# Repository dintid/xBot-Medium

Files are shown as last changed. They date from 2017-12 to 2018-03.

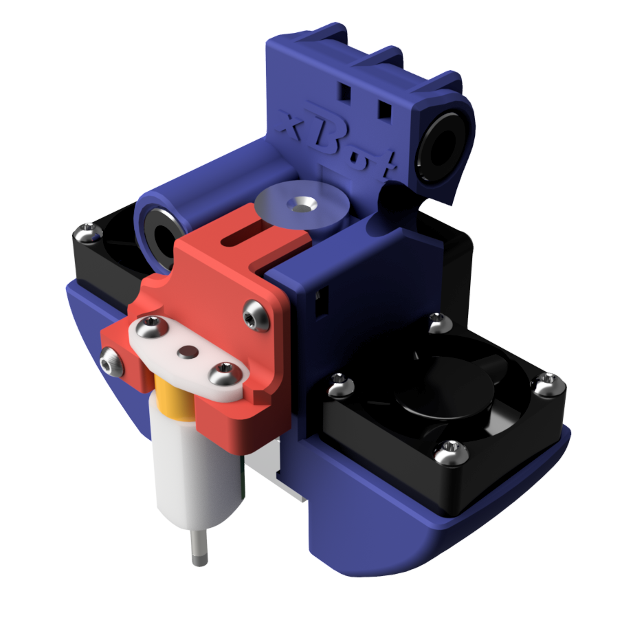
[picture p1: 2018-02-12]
Source files/Printed Parts/E3D carriage/Renders/xBot-Medium Carriage render front.png

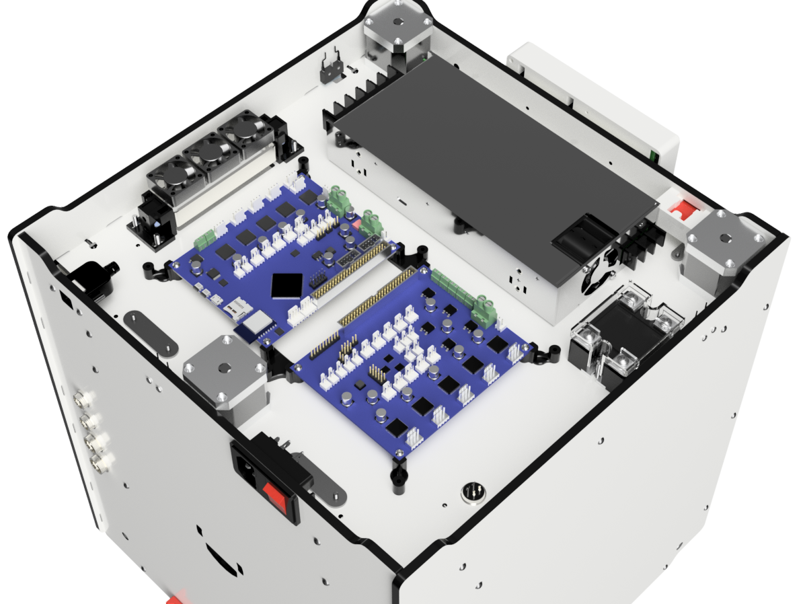
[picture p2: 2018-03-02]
Source files/Printed Parts/Printed Parts render/xBot Medium Bottom.png

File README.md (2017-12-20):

# xBot Medium
In this repository you will find the documentation and source files for the xBot Medium 3D printer. If you are missing a part or information on anything, please feel free to file an issue or contact me via my website at betrue3d.dk

Direct link to first descriptive blog-post:
https://betrue3d.dk/xbot-medium-a-new-printer-is-baking/

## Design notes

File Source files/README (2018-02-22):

Here you'll find all the custom source files for the project in .STP and .PDF format. 

The PDF files are mainly self explananatory while you will need the .STP files for the majority of the actual measurements.
Some PDF files contains information on threads, like the Z-gantry and brackets for the Z-rods.

The .STP files for the frame will be uploaded this week (week 8)

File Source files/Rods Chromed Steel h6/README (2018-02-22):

Here you'll find all the steel RODS we use for the xBot-Medium

The .STP files for the RODS are mostly just in place for the sake of it.

The PDF files contains all relevant measurements for the rods.

Do use some high quality Ground Steel h6 rods and not some generic "chromed steel" bars from china.

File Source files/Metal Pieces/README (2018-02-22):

The various metal/aluminium pieces are found in here.

I've intended the Motorshields to be made in material 0.5-1mm thickness. 
As long as the outer measurements are the same, the thickness doesn't really matter.

There are 2 different versions of the Z 8mm and Z 12mm endcaps:
I did this as it can be hard to find someone who can make these small pieces in steel.

1) First version are made up of 2mm thick steel brackets.
2) Second version are made up of 4mm thick aluminium brackets.

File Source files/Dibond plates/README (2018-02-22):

The plates used to build the frame of the xBot Medium printer

The PDF files are mostly descriptive in nature, where you'll use the .STP files for the actual measurements.

Remember there are lots of partical cuts, so you need a CNC facility who can handle this kind of compound material.

NOTE:
The Door for the front is a cut out part of the TOP frane piece.
The rear Z-Gantry shield is a cut out part of the FRONT frame piece.

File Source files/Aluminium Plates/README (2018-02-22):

# Custom aluminium parts for the xBot Medium printer:

Z-Stage/Z-Gantry lift plate
and
Optionally the Heated platform itself. 

You can use an Ultimaker 2 bed, as they have the same size. 

I recommend a nice AC silicone heater from Keenovo though. You can get them with build in Thermocoupler or PT100 sensor if you ask for it.
Keenovo have even talked about being able to build in PT1000 sensor, which doesn't require a daughterboard on the Duet!

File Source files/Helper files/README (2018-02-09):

In this directory you can find listings of various "other" items like dimensions and wiring of front LED, but also lenght and pin-layout of wiring harness to carriage and similar.
I will be creating these files as I finish them up as "final" and measure them up.

I can unveil the longest run of wireharness from the rear GX plugs up to carriage will be 100cm if you have configured your printer with the maxium distance possible, where you have a 3mm extruder placed at the opposite side of the GX connectors, so you have to route the wireharness across the printer and then along the Bowden tubing.
The 100cm is including the extra 5cm going into twisting the wires.

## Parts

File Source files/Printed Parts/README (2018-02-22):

Here you'll find the parts we need to print for the xBot-Medium printer.

You can also find these objects in a Collection I made on Thingiverse:
https://www.thingiverse.com/dintid/collections/xbot-3d-printer

I have tested and used all these objects.

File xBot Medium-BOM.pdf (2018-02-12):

## xBot-Medium BOM

by Morten Nielsen aka BeTrue3D and Dintid

## Bill Of Materials

All prices are approximate without shipping and will change over time.
The total price is the absolute highest possible price.
You can easily shave off €500 by using different heated bed, duex2 instead of duex5 etc.

Custom Parts:
https://betrue3d.dk/xbot-medium-look-at-materials-custom-bom/
Electronics and Electrical Parts https://betrue3d.dk/xbot-medium-electronics-and-electrical-parts-bom-cont/ Mechanical Parts
https://betrue3d.dk/xbot-medium-mechanical-parts-bom-cont/

## Parts for Dibond frame

Name | Amount | Price # | Price total | Total
xBot Back | 1 | € 45,00 | € 45,00
xBot Bottom | 1 | € 45,00 | € 45,00
xBot Front | 1 | € 45,00 | € 45,00
xBot Left | 1 | € 45,00 | € 45,00
xBot Right | 1 | € 45,00 | € 45,00
xBot Top | 1 | € 45,00 | € 45,00
Total | € 270,00 | € 270,00

## Steel Rods

Name | Amount | Price # | Price Total
X-Rods 8mm 367mm | 2 | € 5,02 | € 10,04
Y-Rods 8mm 358mm | 2 | € 4,90 | € 9,80
Z-Rods 8mm 339mm | 2 | € 4,66 | € 9,32
Z-Rods 12mm 339mm | 2 | € 5,66 | € 11,32
X-Rod 6mm 327mm | 1 | € 4,50 | € 4,50
Y-Rod 6mm 302mm | 1 | € 4,18 | € 4,18
Shipping DHL | 1 | € 19,00 | € 19,00
Total | € 68,16 | € 68,16

## Metal/steel Parts

Name | Amount | Price # | Price Total
Left Motorshield | 1 | € 0,00
Right Motorshield | 1 | € 0,00
Z-8mm Rod Plates* | 2 | € 0,00
Z-12mm Rod Plates* | 2 | € 0,00
* If you can't get steel brackets, you can use 4mm thick aluminium instead. See below

## Aluminium Parts

Name | Amount | Price # | Price Total
5mm PEI Coated printbed
257x229x5mm*
1 | € 54,00 | € 54,00

Z-Liftplate | 1 | € 45,00 | € 45,00
Total | € 99,00 | € 99,00
* You can use a heatbed from Ultimaker 2.

### Electronics and electrics

Name | Amount | Price # | Price Total
Duet Wifi | 1 | € 162,30 € 162,30
Duex 2/5* | 1 | € 116,60 € 116,60
Thermocoupler Daughterboard** | 1 | € 31,00 | € 31,00
PT100 Daughterboard | 1 | € 31,00 | € 31,00
PanelDue 4.3"*** | 1 | € 99,89 | € 99,89
BLTouch SMART | 1 | € 39,90 | € 39,90
Heated Bed**** | 1 | € 54,00 | € 54,00
AC Silicone heater 500w | 1 | € 40,50 | € 40,50
SSR DC-AC | 1 | € 4,00 | € 4,00
Chamber Heater 200w Ceramic PTC Heater | 1 | € 4,75 | € 4,75
24v 30mm fans for Chamber Heater | 3 | € 1,21 | € 3,63
12v 30mm Fans for Printed Objects | 2 | € 2,08 | € 4,16
Powersupply HPR-450-24 or similar | 1 | € 60,00 | € 60,00
LED - RGB | 1 | € 11,25 | € 11,25
Front USB Power 5v 3a | 1 | € 1,12 | € 1,12
Rear USB Port | 1 | € 1,79 | € 1,79
Total | € 665,89 | € 665,89
* Price listed is for Duex5
** You can do with just 1 and use Thermistor instead or even PT1000 (with 3x zeros) without daughterboard *** Not really necesary. There is not room for 7".
**** 5mm Aluplate or use UM2 heated bed.

### Various electrical mechanical parts

Name | Amount | Price # | Price Total
Manual on-off switch | 1 | € 1,00 | € 1,00
Limit Switch - Long Arm | 2 | € 1,12 | € 2,24
Limit Switch - Short Arm | 3 | € 1,15 | € 3,45
AC Power plug on/off | 1 | € 1,12 | € 1,12
GX12-2-pin | 1 | € 1,00 | € 1,00
GX12 4-pin | 6 | € 1,00 | € 6,00
GX12-5-pin | 1 | € 1,00 | € 1,00
GX16 8-pin | 1 | € 1,00 | € 1,00
GX16 6-pin | 1 | € 1,00 | € 1,00
GX16 5-pin | 1 | € 1,00 | € 1,00
Total | € 18,81 | € 18,81

## Motors

Name | Amount | Price # | Price Total

Nema 17 w. 280 lead screw
SKU: 17HS3001-280N
| 3 | € 26,70 | € 80,10
X and Y Motors SKU:17HM18- 2004S | 2 | € 11,90 | € 23,80
Extruder Motors * SKU:17HM18-2004S | 1 | € 11,90 | € 11,90
Extruder Motors * SKU:17HM08-1204S | 2 | € 9,90 | € 19,80
Total | € 135,60 | € 135,60
* For 2.85/3mm filament
** For 1,75mm filament

### Hotend and parts

Name | Amount | Price # | Price Total
E3Dv6 Full 1,75mm Bowden | 1 | € 63,60 | € 63,60
PT100 sensor | 1 | € 12,50 | € 12,50
Plated 0.4mm Copper Nozzle | 1 | € 11,75 | € 11,75
Heater Cartridge 40w | 1 | € 5,40 | € 5,40
Total | € 93,25 | € 93,25

### Mechanical Parts other

Name | Amount | Price # | Price Total
200GT-2 Belts | 2 | € 0,33 | € 0,66
20-GT2 Pulley 5mm Bore | 2 | € 1,33 | € 2,66
20-GT2 Pulley 8mm Bore | 10 | € 0,66 | € 6,60
610-GT2 Belts | 4 | € 0,75 | € 2,98
Sliders å bushing + spring | 4 | € 2,15 | € 8,60
Bag of Spacers 8mm Bore | 1 | € 4,70 | € 4,70
F688 Flanged Bearings | 8 | € 0,42 | € 3,32
Anti Backblash Nut | 3 | € 2,49 | € 7,46
LMK12LUU Flanged Bearings | 2 | € 2,32 | € 4,64
LM8UU Flanged Bearings | 2 | € 2,07 | € 4,14
Fingerscrews sets of fingerscrew, spring, spacer | 3 | € 1,13 | € 3,39
LM6LUU | 2 | € 1,58 | € 3,16
Total | € 52,31 | € 52,31

### Screws, Nuts Etc

Name | Amount | Price # | Price Total
m3 8mm Button Head | 10
m3 10mm Button Head | 64
m3 10mm Socket Head | 4
m3 12mm Button Head | 21
m3 16mm Button Head | 61
m3 20mm Button Head | 6
m3 30mm Button Head | 8
m3 20mm Flat Head (countersunk) | 3
m3 Spacer | 8

m3 Square Nuts | 45
m3 Nuts

4
m4 10mm Button Head

4
m4 12mm Button Head

8
m4 20mm Button Head

6
m4 Spacer

8
Wires
Connectors
Heatshrink
Wirewrap
Total Approximate | € 40,00 | € 40,00
Totalling: | | € 1.443,02

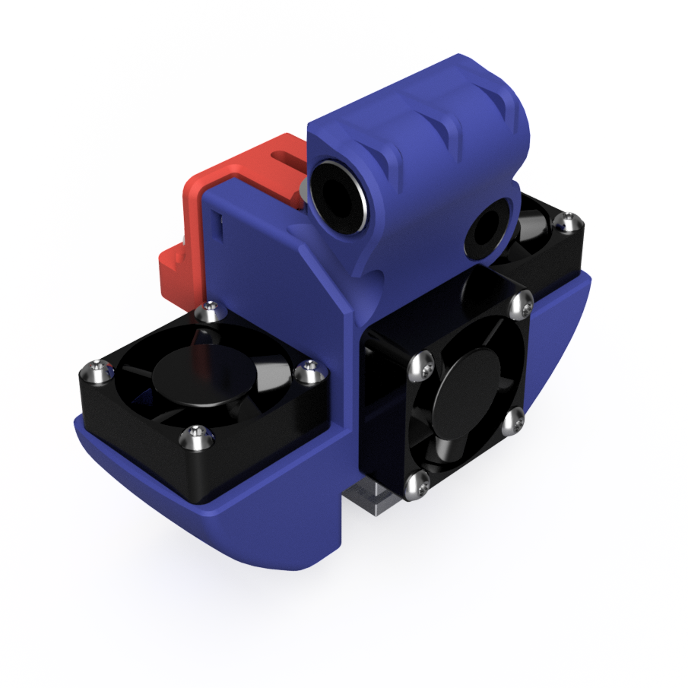
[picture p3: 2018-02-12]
Source files/Printed Parts/E3D carriage/Renders/xBot-Medium Carriage render rear.png

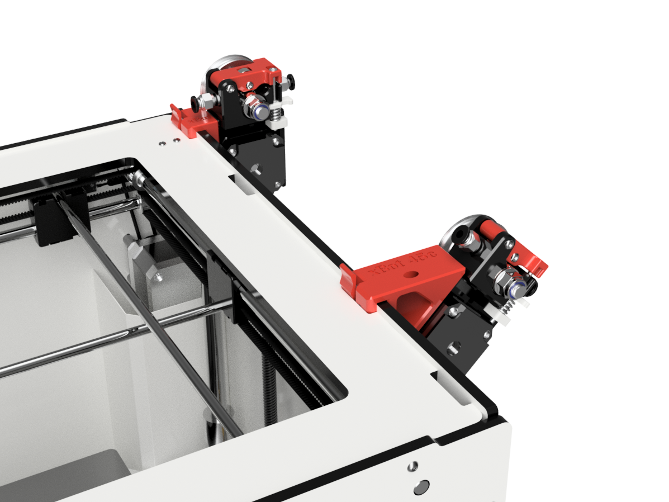
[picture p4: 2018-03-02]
Source files/Printed Parts/Printed Parts render/xBot Medium Clip-On-show.png

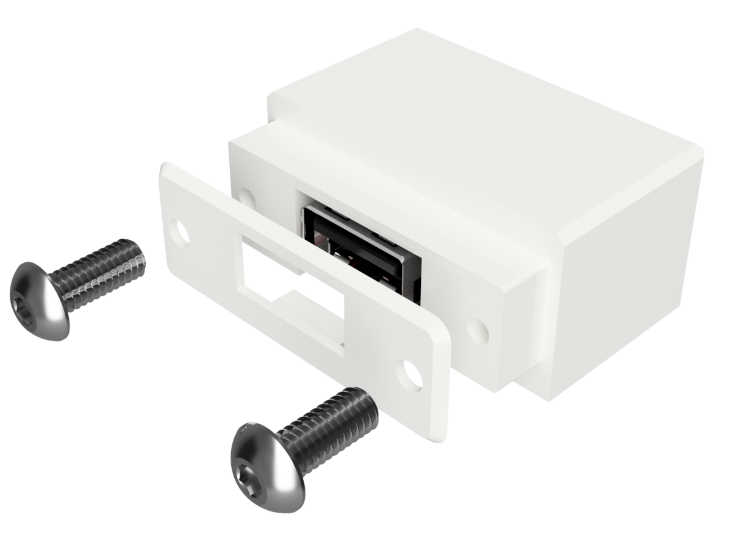
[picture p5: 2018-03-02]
Source files/Printed Parts/Printed Parts render/USB front mount v8.png

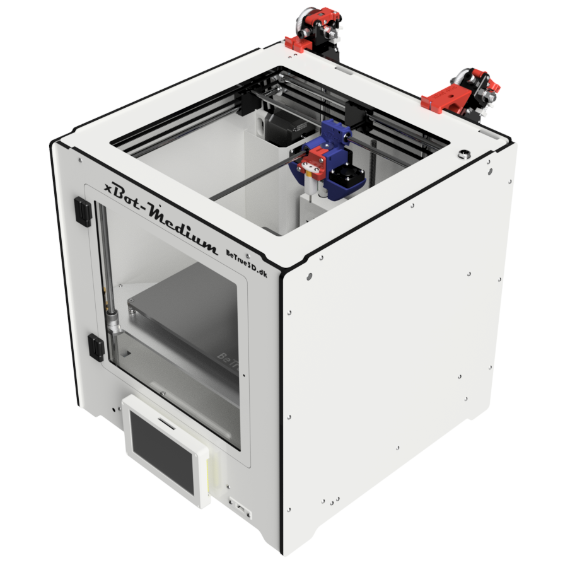
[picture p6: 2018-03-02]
Source files/Printed Parts/E3D carriage/xBot Medium render mid feb.png

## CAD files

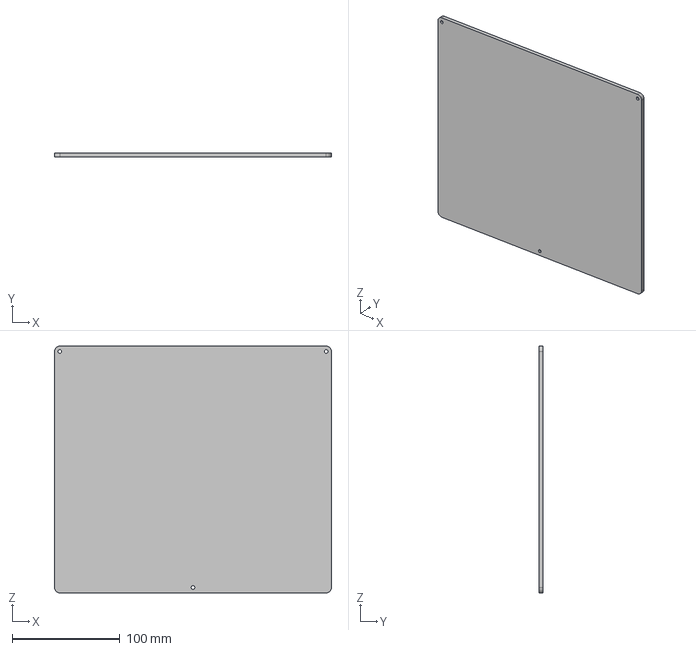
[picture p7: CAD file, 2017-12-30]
Source files/Aluminium Plates/Heatplate.stp
257.0 x 4.00 x 229.0 mm

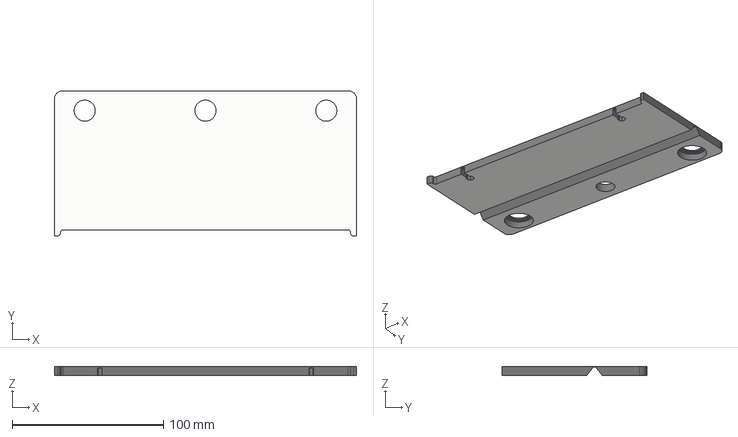
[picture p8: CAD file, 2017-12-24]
Source files/Dibond plates/Z-Rod Shield Rear - Reference only.stp
200.0 x 96.0 x 6.00 mm

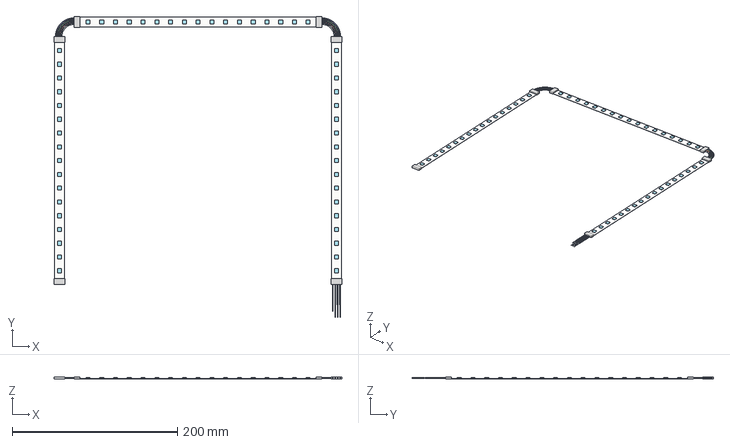
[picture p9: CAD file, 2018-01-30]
Source files/Helper files/xBot Medium - Front LED.stp
348.5 x 364.3 x 3.00 mm

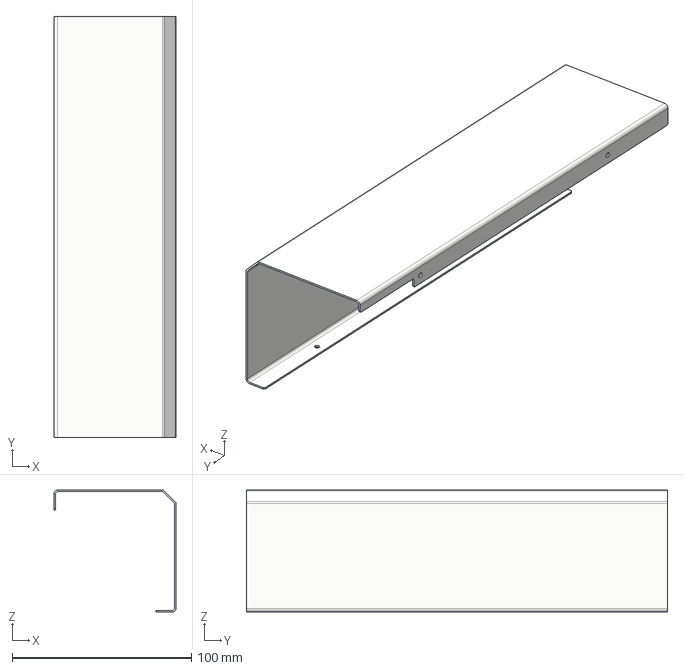
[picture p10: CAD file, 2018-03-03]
Source files/Metal Pieces/MotorShield x2.step
68.0 x 235.0 x 68.0 mm

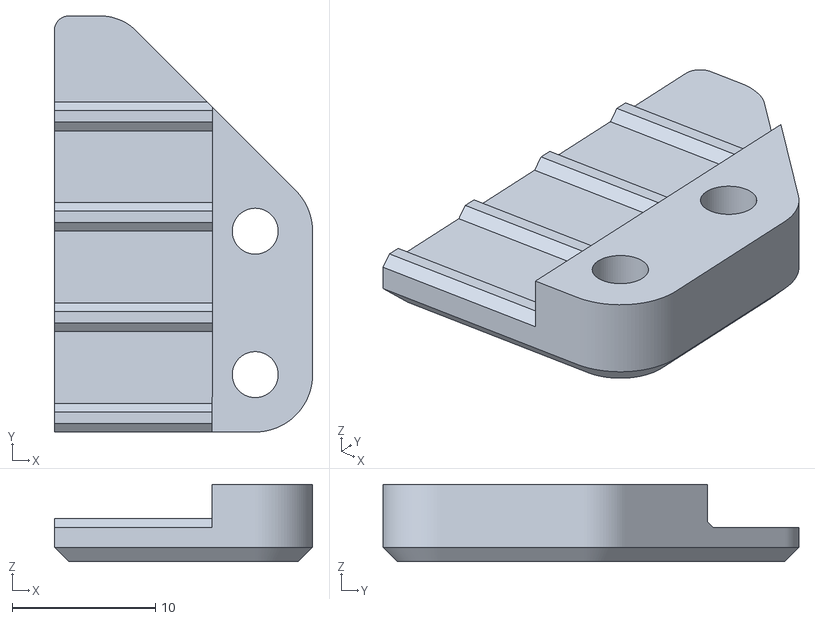
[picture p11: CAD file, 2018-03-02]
Source files/Printed Parts/Bed Wire Relief/Bed-Wire Relief.stl
18.0 x 29.0 x 5.40

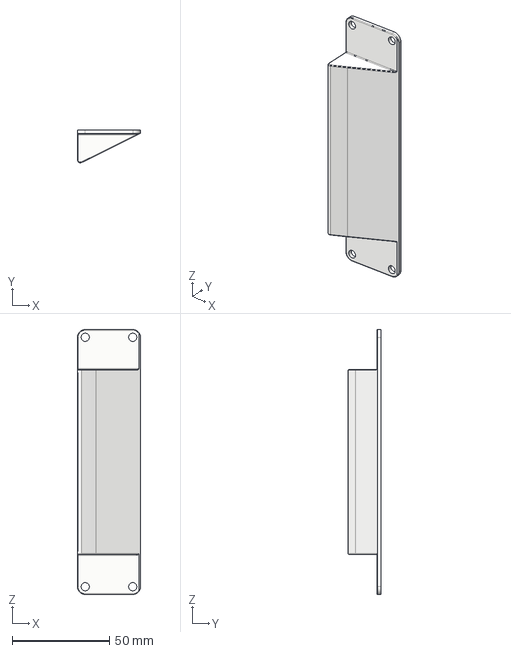
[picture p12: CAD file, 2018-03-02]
Source files/Printed Parts/Chamber Heater/Chamber heater fanduct.stp
32.4 x 16.8 x 136.0 mm

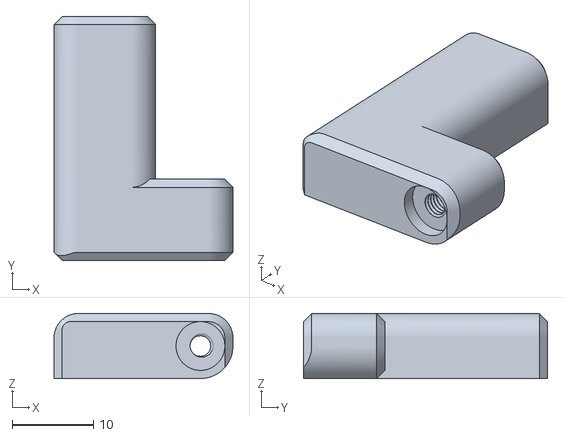
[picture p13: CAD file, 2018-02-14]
Source files/Printed Parts/Door Hinges/Hinge Frame.stl
22.0 x 30.0 x 8.00

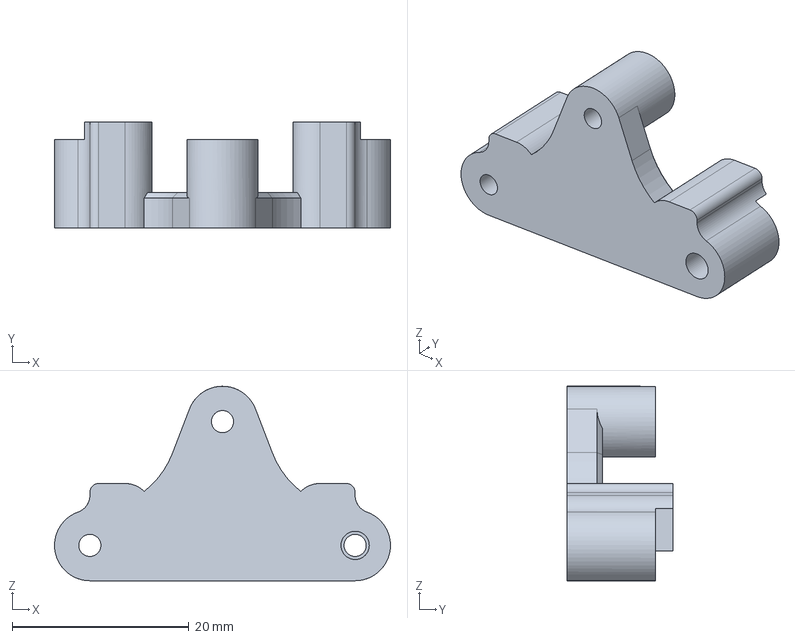
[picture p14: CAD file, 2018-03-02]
Source files/Printed Parts/Duet-Duex Mounting parts/DuetDuex xBot Mounting x2.stp
38.0 x 12.0 x 22.0 mm

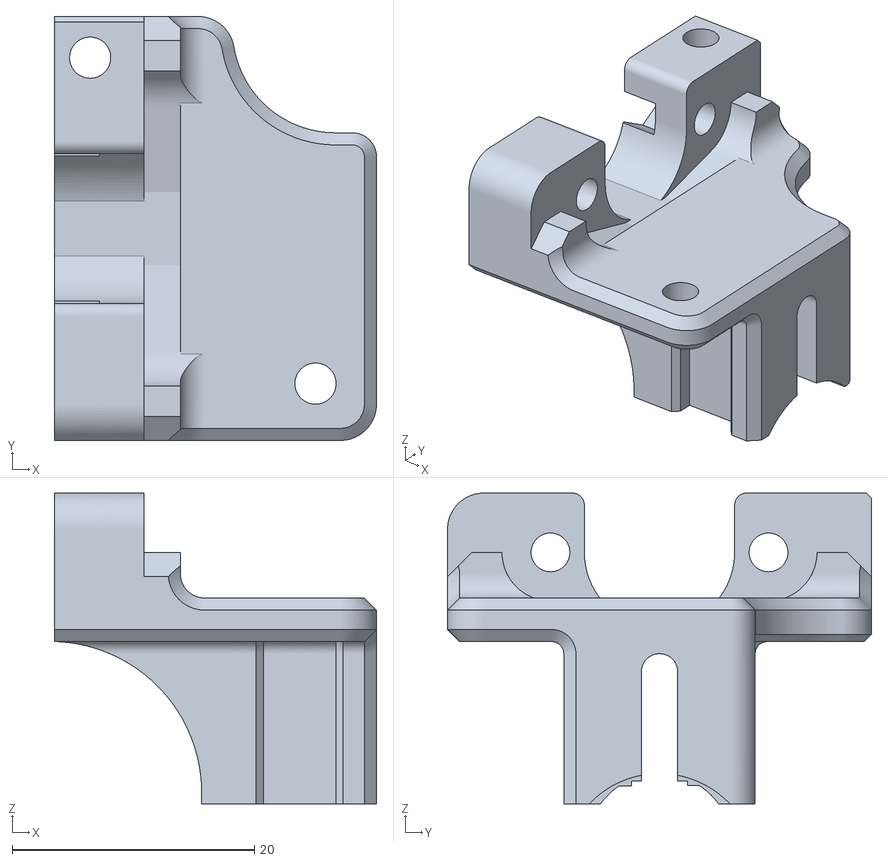
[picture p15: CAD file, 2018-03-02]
Source files/Printed Parts/E3D carriage/xBot BLTouch-Mount_Hotend-Clamp.stl
26.6 x 35.0 x 25.7

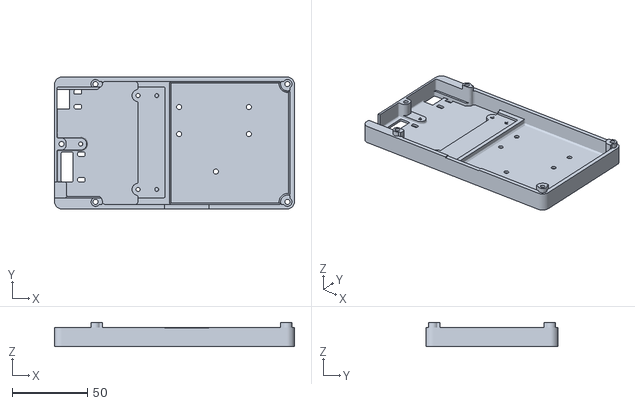
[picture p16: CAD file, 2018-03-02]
Source files/Printed Parts/PD5 Compact w hidden wires for v2 and v3 PCB/PD5 Compact Back w hidden wires for v2 and v3 PCB.stl
159.9 x 87.9 x 16.3

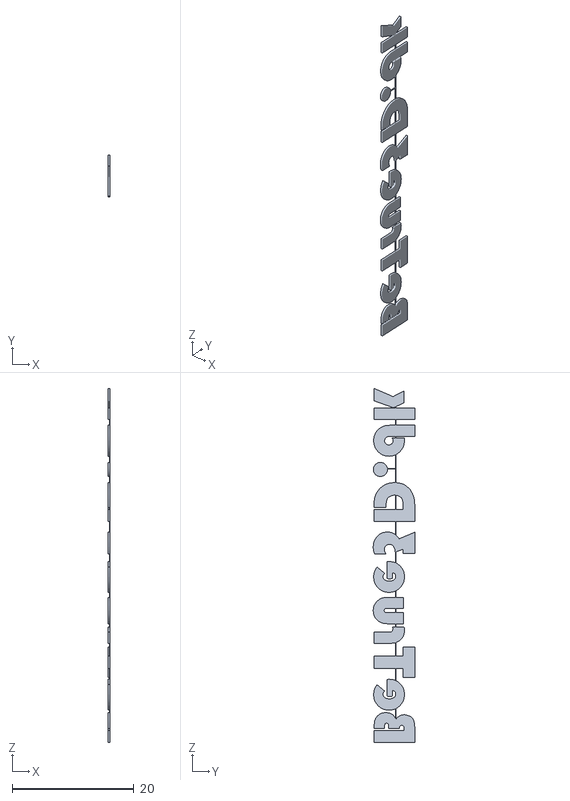
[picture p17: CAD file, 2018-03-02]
Source files/Printed Parts/Text/BeTrue3D.stl
0.3 x 6.83 x 58.0

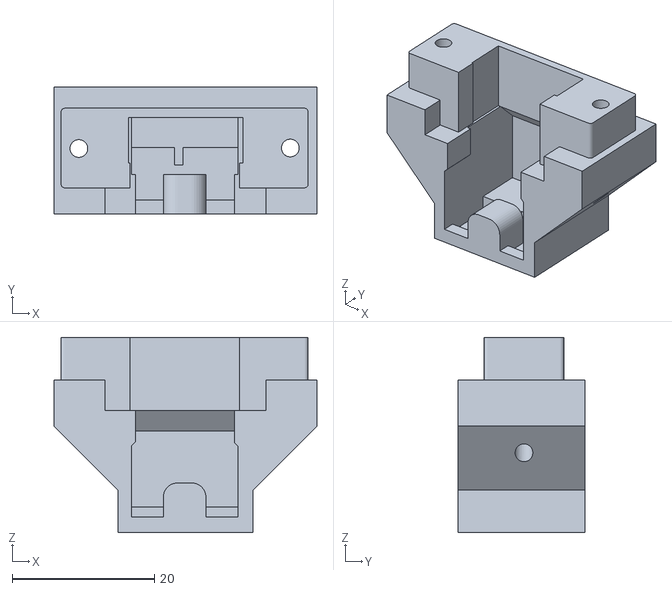
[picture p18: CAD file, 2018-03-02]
Source files/Printed Parts/USB Mount front/USB Front Mount -Inside.stl
37.0 x 17.9 x 27.5

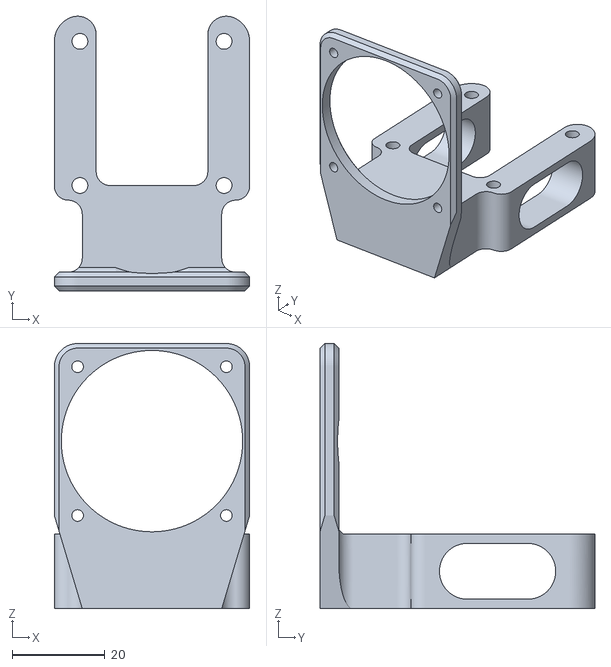
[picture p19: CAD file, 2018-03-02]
Source files/Printed Parts/XY Motor mounts/XY Motor Mount w fan.stl
42.0 x 59.1 x 57.0

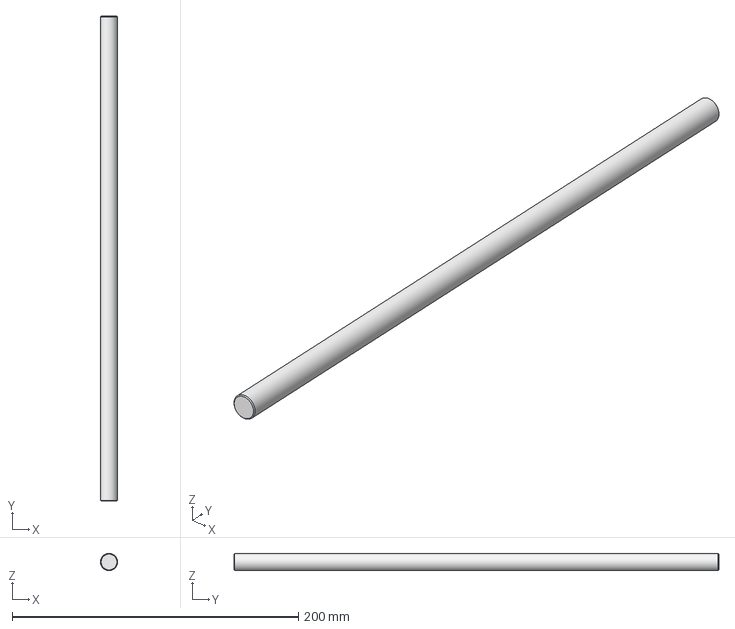
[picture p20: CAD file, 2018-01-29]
Source files/Rods Chromed Steel h6/Z-12mm_339mm rods x2.stp
12.0 x 339.0 x 12.0 mm

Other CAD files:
Source files/Aluminium Plates/Z-Lift Plate xBot Medium.stp
Source files/Metal Pieces/Z-8mm Rod-Plates - 4mm thick alux2.stp
Source files/Printed Parts/Chamber Heater/Guard-Chamber Heater and FanShroud for x3 Fans.stp
Source files/Metal Pieces/Z-12mm rod-plates - 4mm thick alu x2.stp
Source files/Metal Pieces/Z-12mm rod-plates x2.stp
Source files/Metal Pieces/Z-8mm Rod-Plates x2.stp
Source files/Printed Parts/Chamber Heater/Chamber heater fanduct.stl
Source files/Printed Parts/Chamber Heater/Guard-Chamber Heater and FanShroud for x2 Fans.stl
Source files/Printed Parts/Chamber Heater/Guard-Chamber Heater and FanShroud for x3 Fans.stl
Source files/Printed Parts/Door Hinges/Hinge Door.stl
Source files/Printed Parts/Door Hinges/Hinge-Door.stl
Source files/Printed Parts/Door Hinges/Hinge-Frame.stl
Source files/Printed Parts/Duet-Duex Mounting parts/CableHookPSU.stl
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

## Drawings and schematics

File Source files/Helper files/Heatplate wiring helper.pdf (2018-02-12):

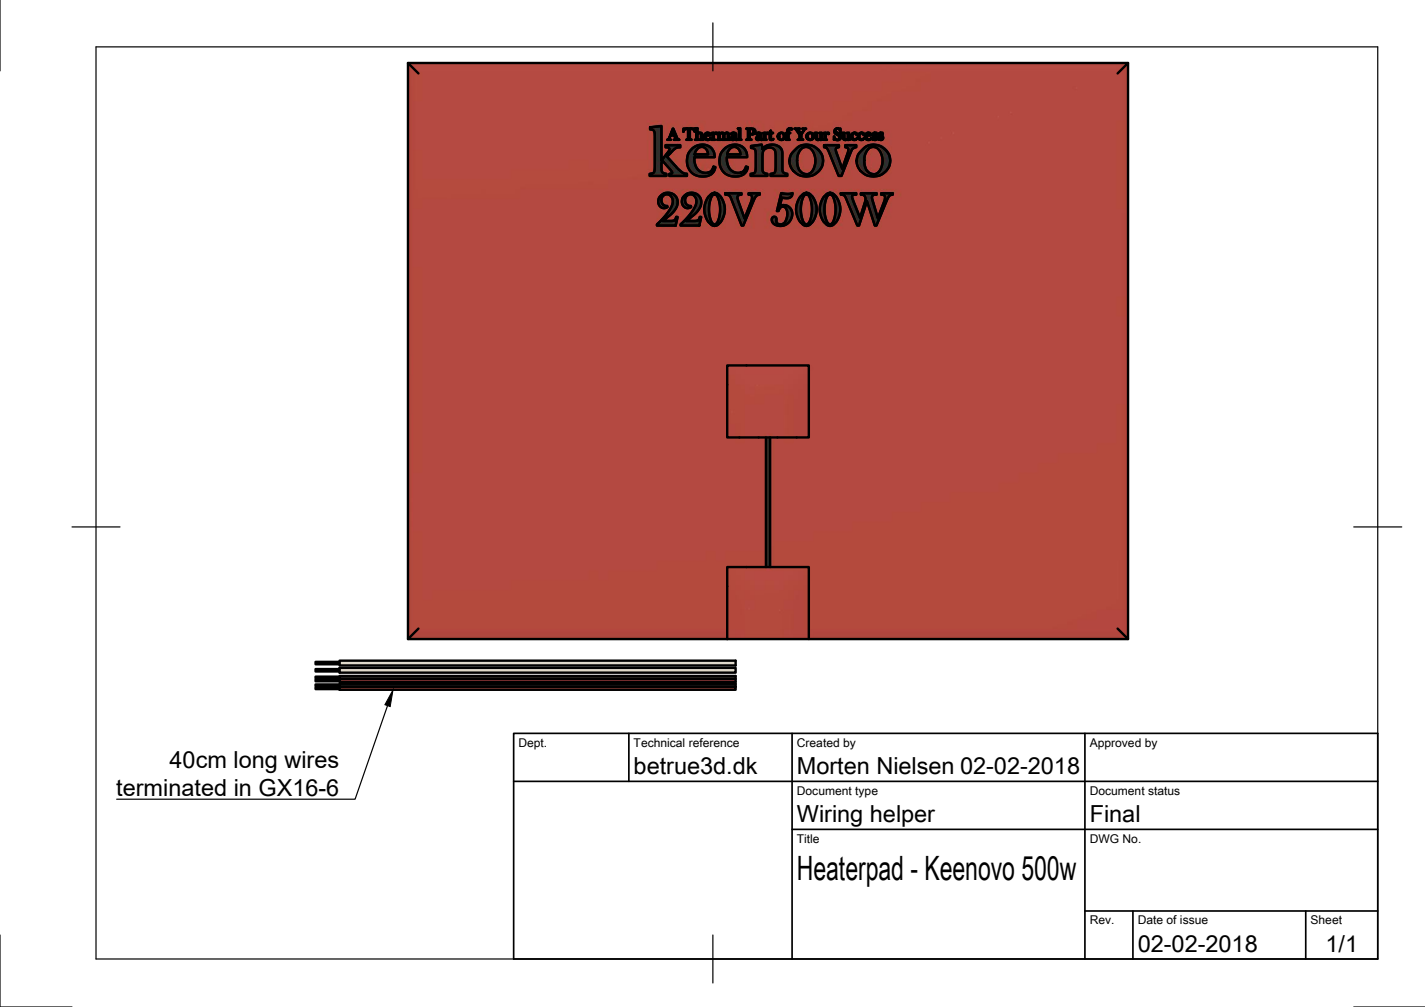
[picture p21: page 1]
terminated in GX16-6

Dept. | Technical reference betrue3d.dk | Created by Morten Nielsen 40cm long wires 02-02-2018 | Approved by

Document type Wiring helper | Document status Final

Title Heaterpad - Keenovo 500w | DWG No.

Rev. | Date of issue 02-02-2018 | Sheet 1/1

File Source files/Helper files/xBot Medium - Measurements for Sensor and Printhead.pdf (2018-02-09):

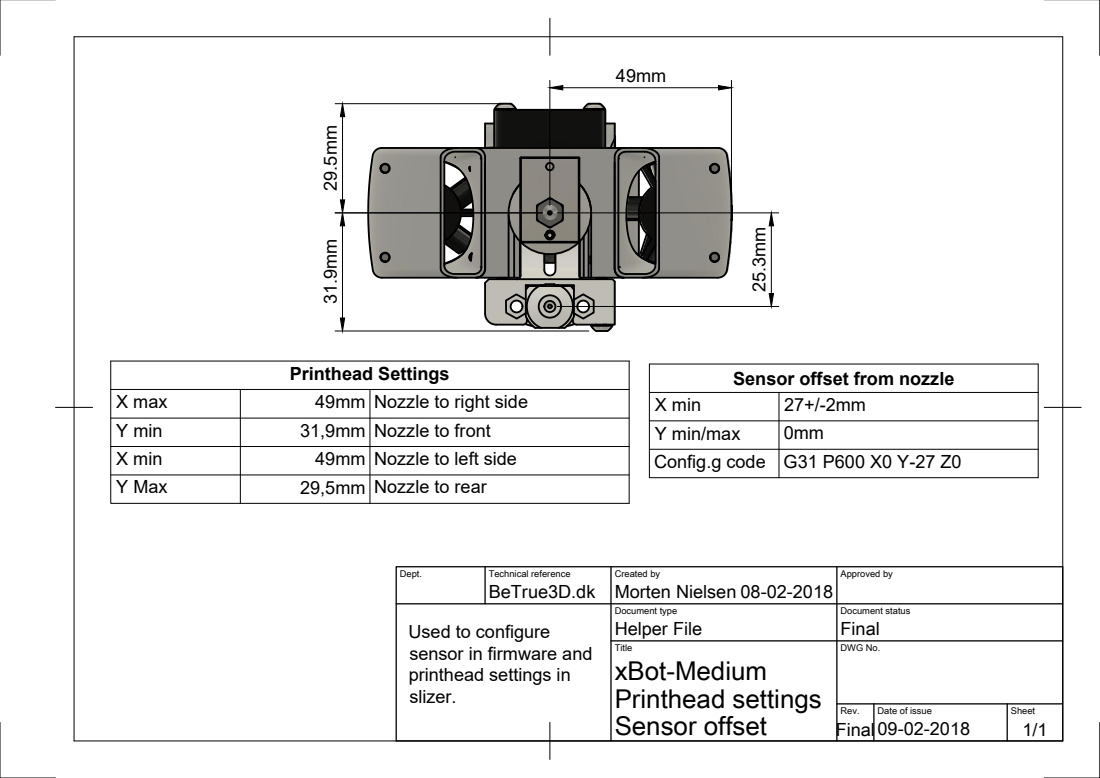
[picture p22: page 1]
BeTrue3D.dk; Morten Nielsen 25.3mm; Printhead Settings; X max; Nozzle to right side; Y min; Nozzle to front; X min; Y min/max

Sensor offset from nozzle

X min | 49mm | Nozzle to left side
Y Max | 29,5mm | Nozzle to rear

Config.g code | G31 P600 X0 Y-27 Z0

Dept. | Technical reference | Created by 08-02-2018 | Approved by

Used to configure sensor in firmware and printhead settings in slizer. | | Document type Helper File | Document status Final

Title xBot-Medium Printhead settings Sensor offset | DWG No.

Rev. Final 09-02-2018 | Date of issue | Sheet 1/1

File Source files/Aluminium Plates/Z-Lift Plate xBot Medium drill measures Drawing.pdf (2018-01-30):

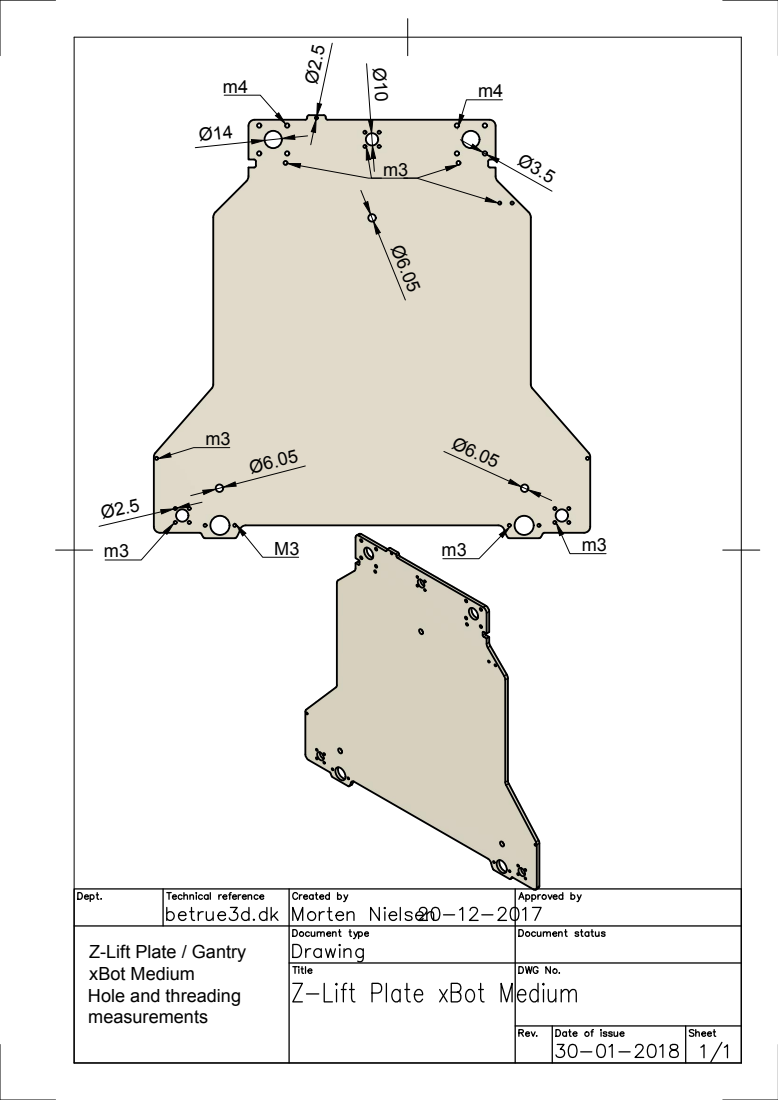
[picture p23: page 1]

Z-Lift Plate / Gantry
xBot Medium
Hole and threading
measurements

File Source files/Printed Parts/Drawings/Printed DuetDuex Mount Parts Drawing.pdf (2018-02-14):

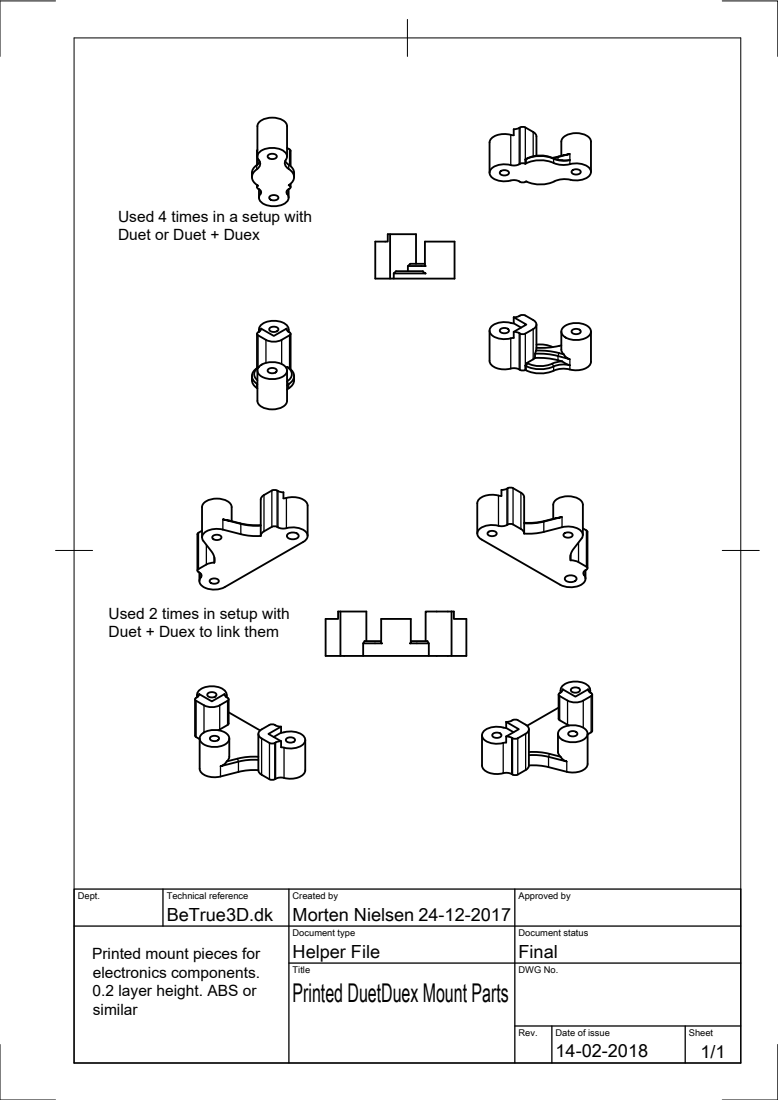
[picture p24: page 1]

Used 4 times in a setup with
Duet or Duet + Duex

Used 2 times in setup with
Duet + Duex to link them

Dept. | Technical reference BeTrue3D.dk | Created by Morten Nielsen 24-12-2017 | Approved by

Printed mount pieces for electronics components. 0.2 layer height. ABS or similar | | Document type Helper File | Document status Final

Title Printed DuetDuex Mount Parts | DWG No.

Rev. | Date of issue 14-02-2018 | Sheet 1/1

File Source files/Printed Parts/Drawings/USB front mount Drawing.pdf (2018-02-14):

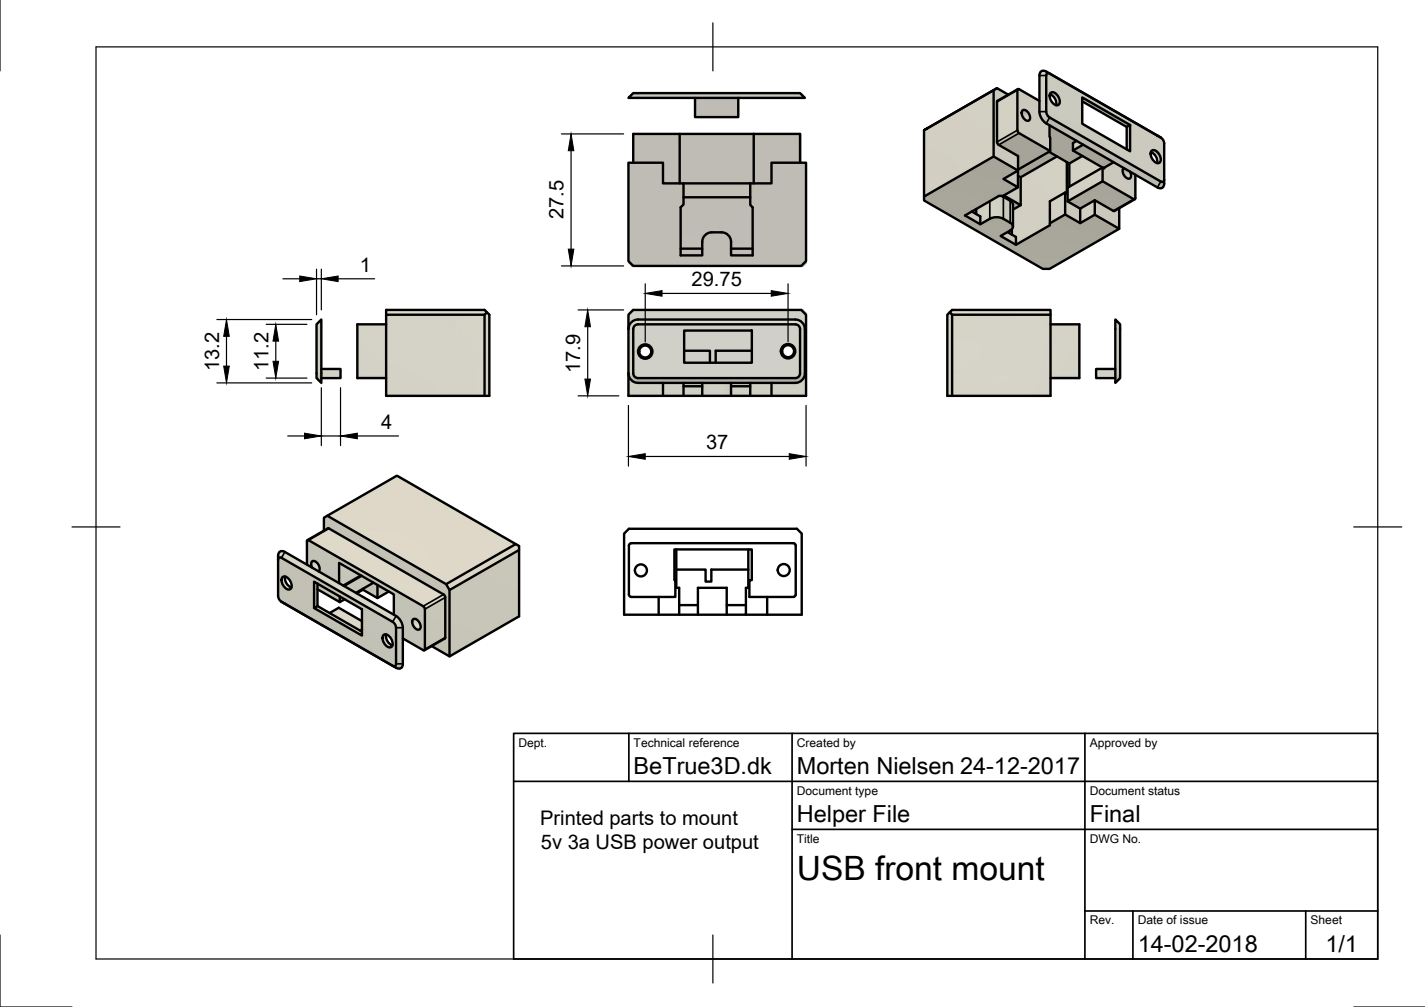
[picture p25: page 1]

Dept. | Technical reference BeTrue3D.dk | Created by Morten Nielsen 24-12-2017 | Approved by

Printed parts to mount 5v 3a USB power output | | Document type Helper File | Document status Final

Title USB front mount | DWG No.

Rev. | Date of issue 14-02-2018 | Sheet 1/1

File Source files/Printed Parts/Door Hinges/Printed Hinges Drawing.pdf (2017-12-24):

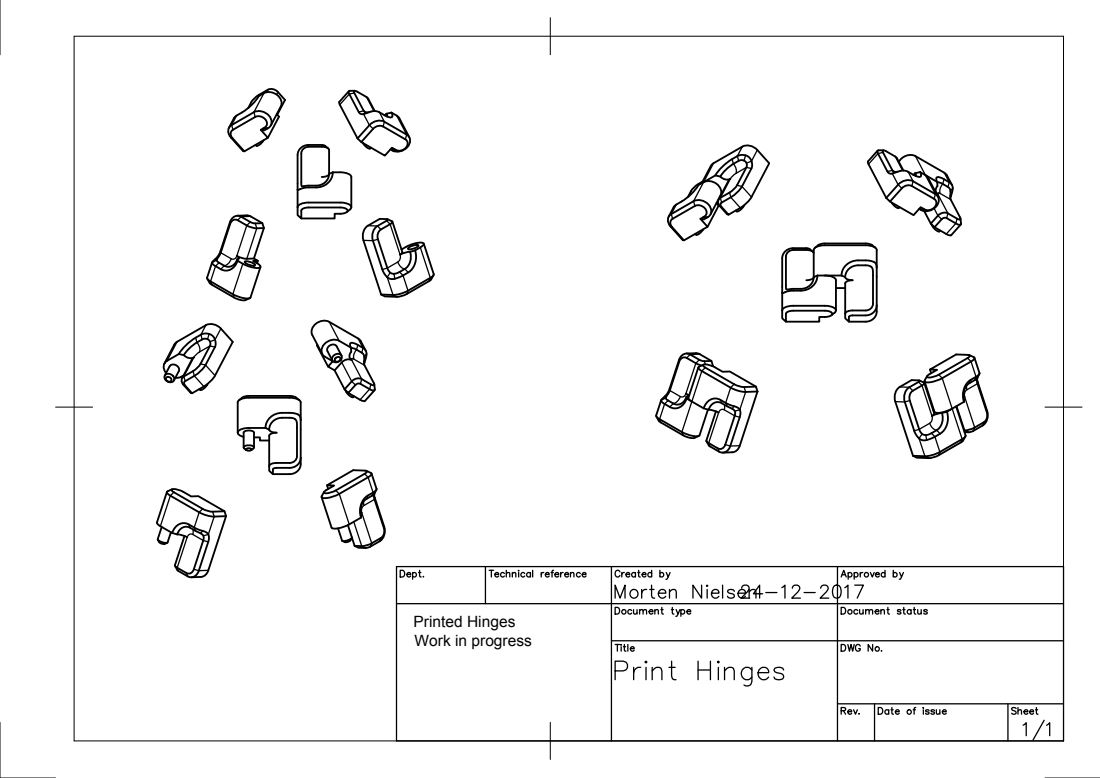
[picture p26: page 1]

Printed Hinges
Work in progress

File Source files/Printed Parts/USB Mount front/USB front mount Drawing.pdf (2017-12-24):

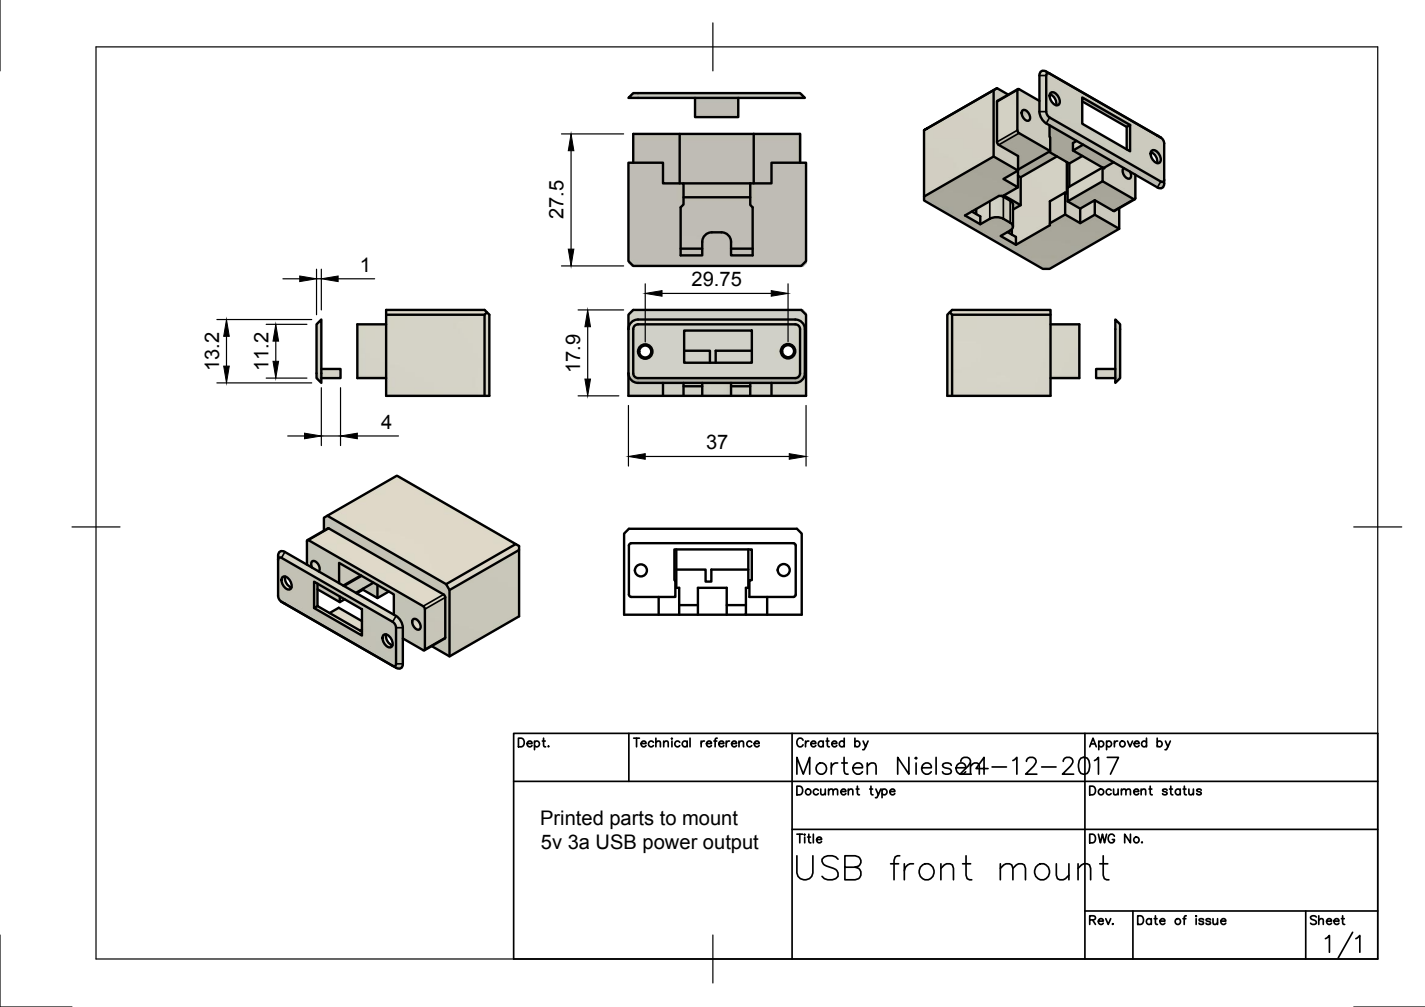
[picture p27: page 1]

Printed parts to mount
5v 3a USB power output

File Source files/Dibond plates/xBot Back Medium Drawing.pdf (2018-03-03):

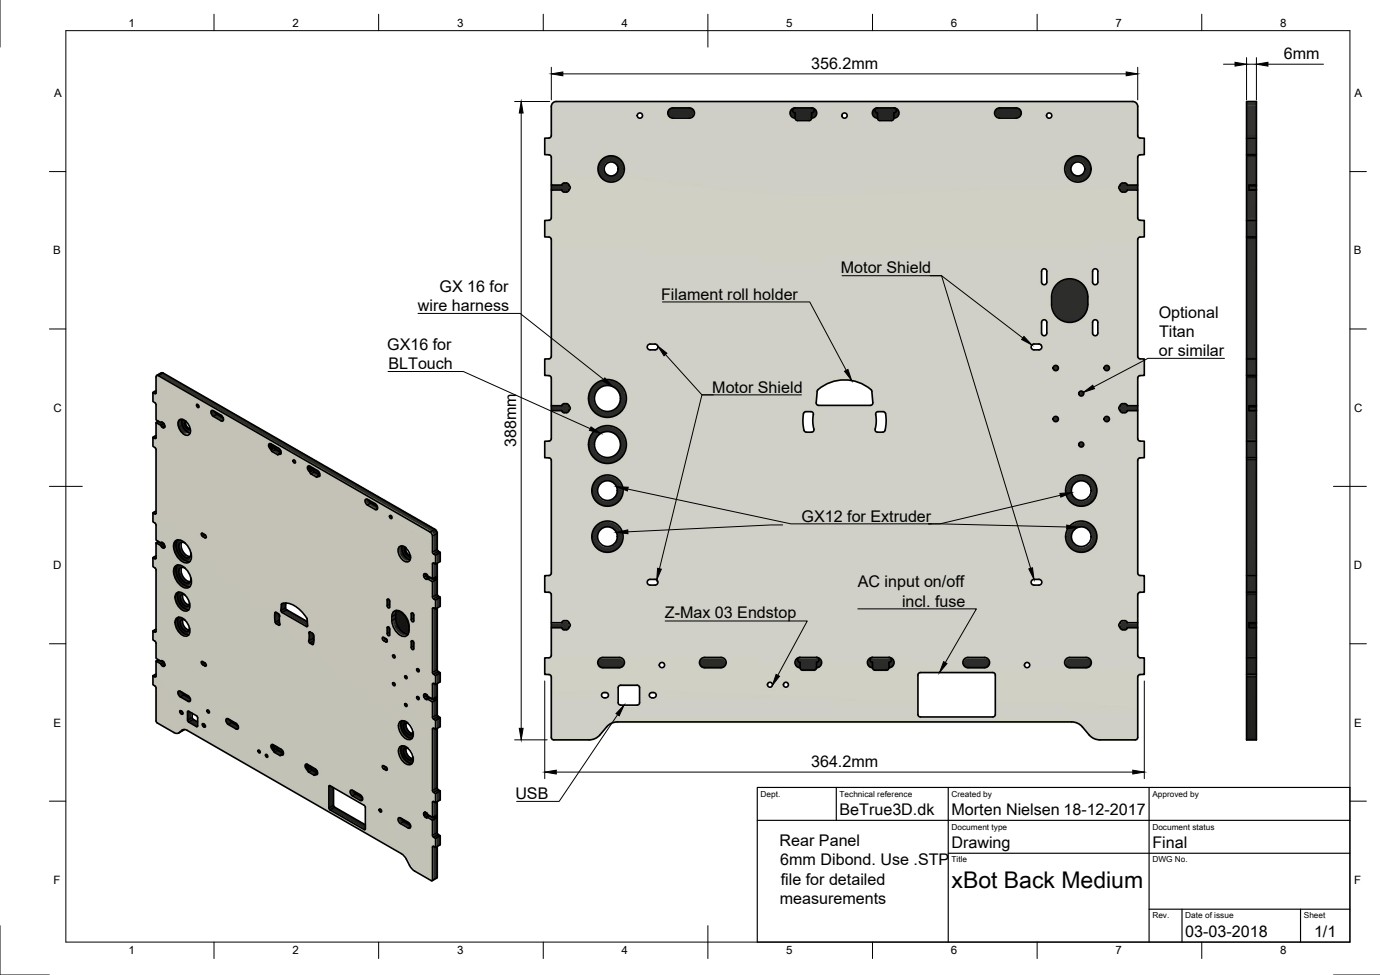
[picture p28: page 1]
or similar; GX 16 for wire harness; GX16 for; GX12 for Extruder; Motor Shield

Filament roll holder

AC input on/off

incl. fuse Z-Max 03 Endstop

Dept. | Technical reference BeTrue3D.dk | Created by Morten Nielsen 18-12-2017 | Approved by

Rear Panel 6mm Dibond. Use .STP file for detailed measurements | | Document type Drawing | Document status Final

Title xBot Back Medium | DWG No.

Rev. | Date of issue 03-03-2018 | Sheet 1/1

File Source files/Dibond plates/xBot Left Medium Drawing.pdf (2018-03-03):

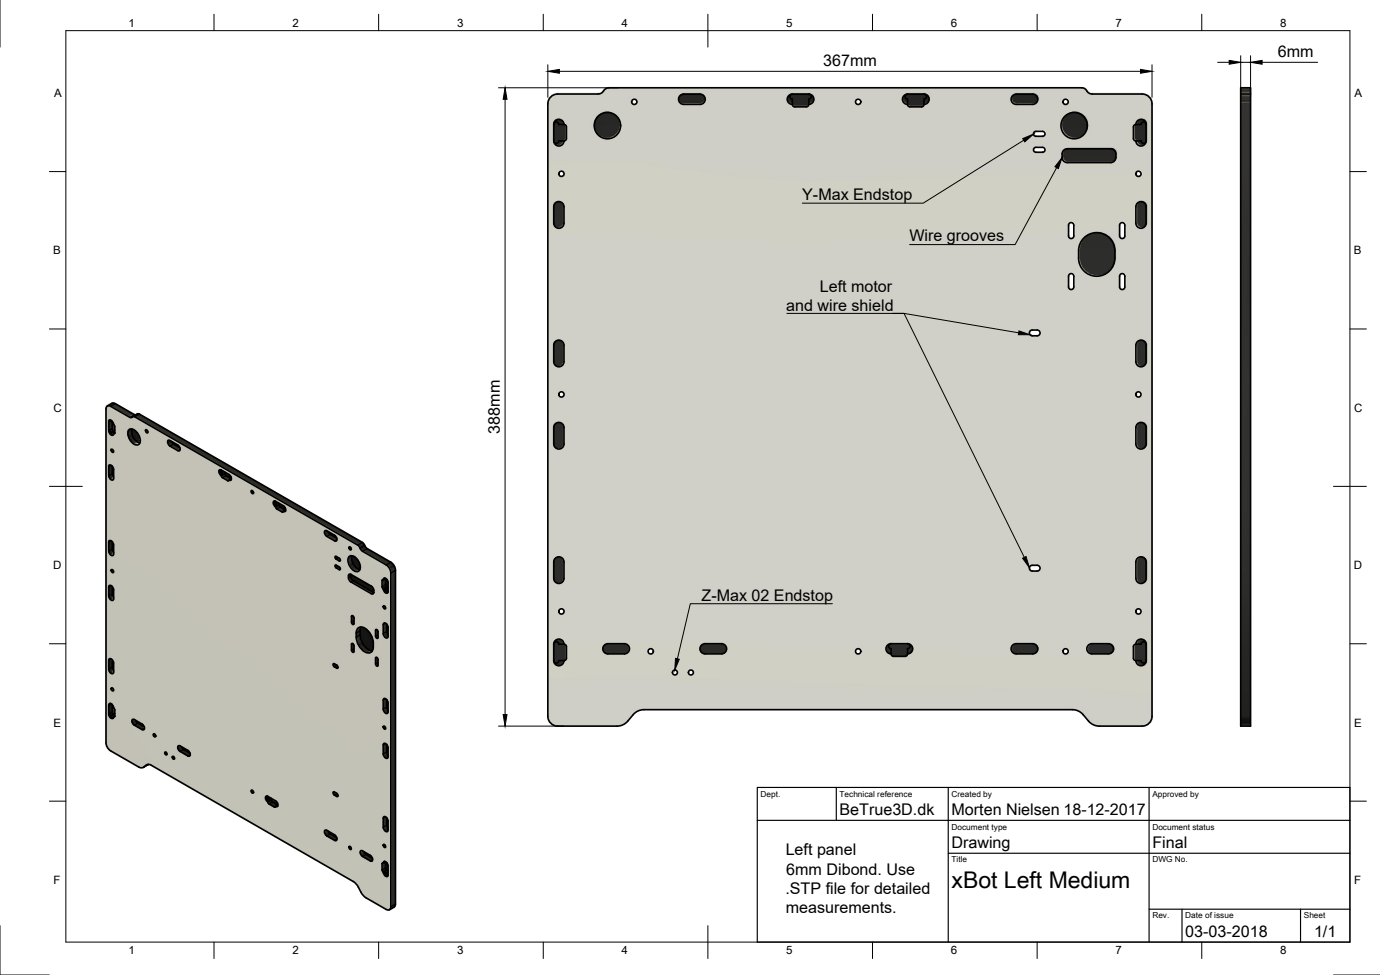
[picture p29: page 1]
BeTrue3D.dk; Morten Nielsen 388mm; Z-Max 02 Endstop; Y-Max Endstop; Wire grooves

Left motor
and wire shield

Dept. | Technical reference | Created by 18-12-2017 | Approved by

Left panel 6mm Dibond. Use .STP file for detailed measurements. | | Document type Drawing | Document status Final

Title xBot Left Medium | DWG No.

Rev. | Date of issue 03-03-2018 | Sheet 1/1

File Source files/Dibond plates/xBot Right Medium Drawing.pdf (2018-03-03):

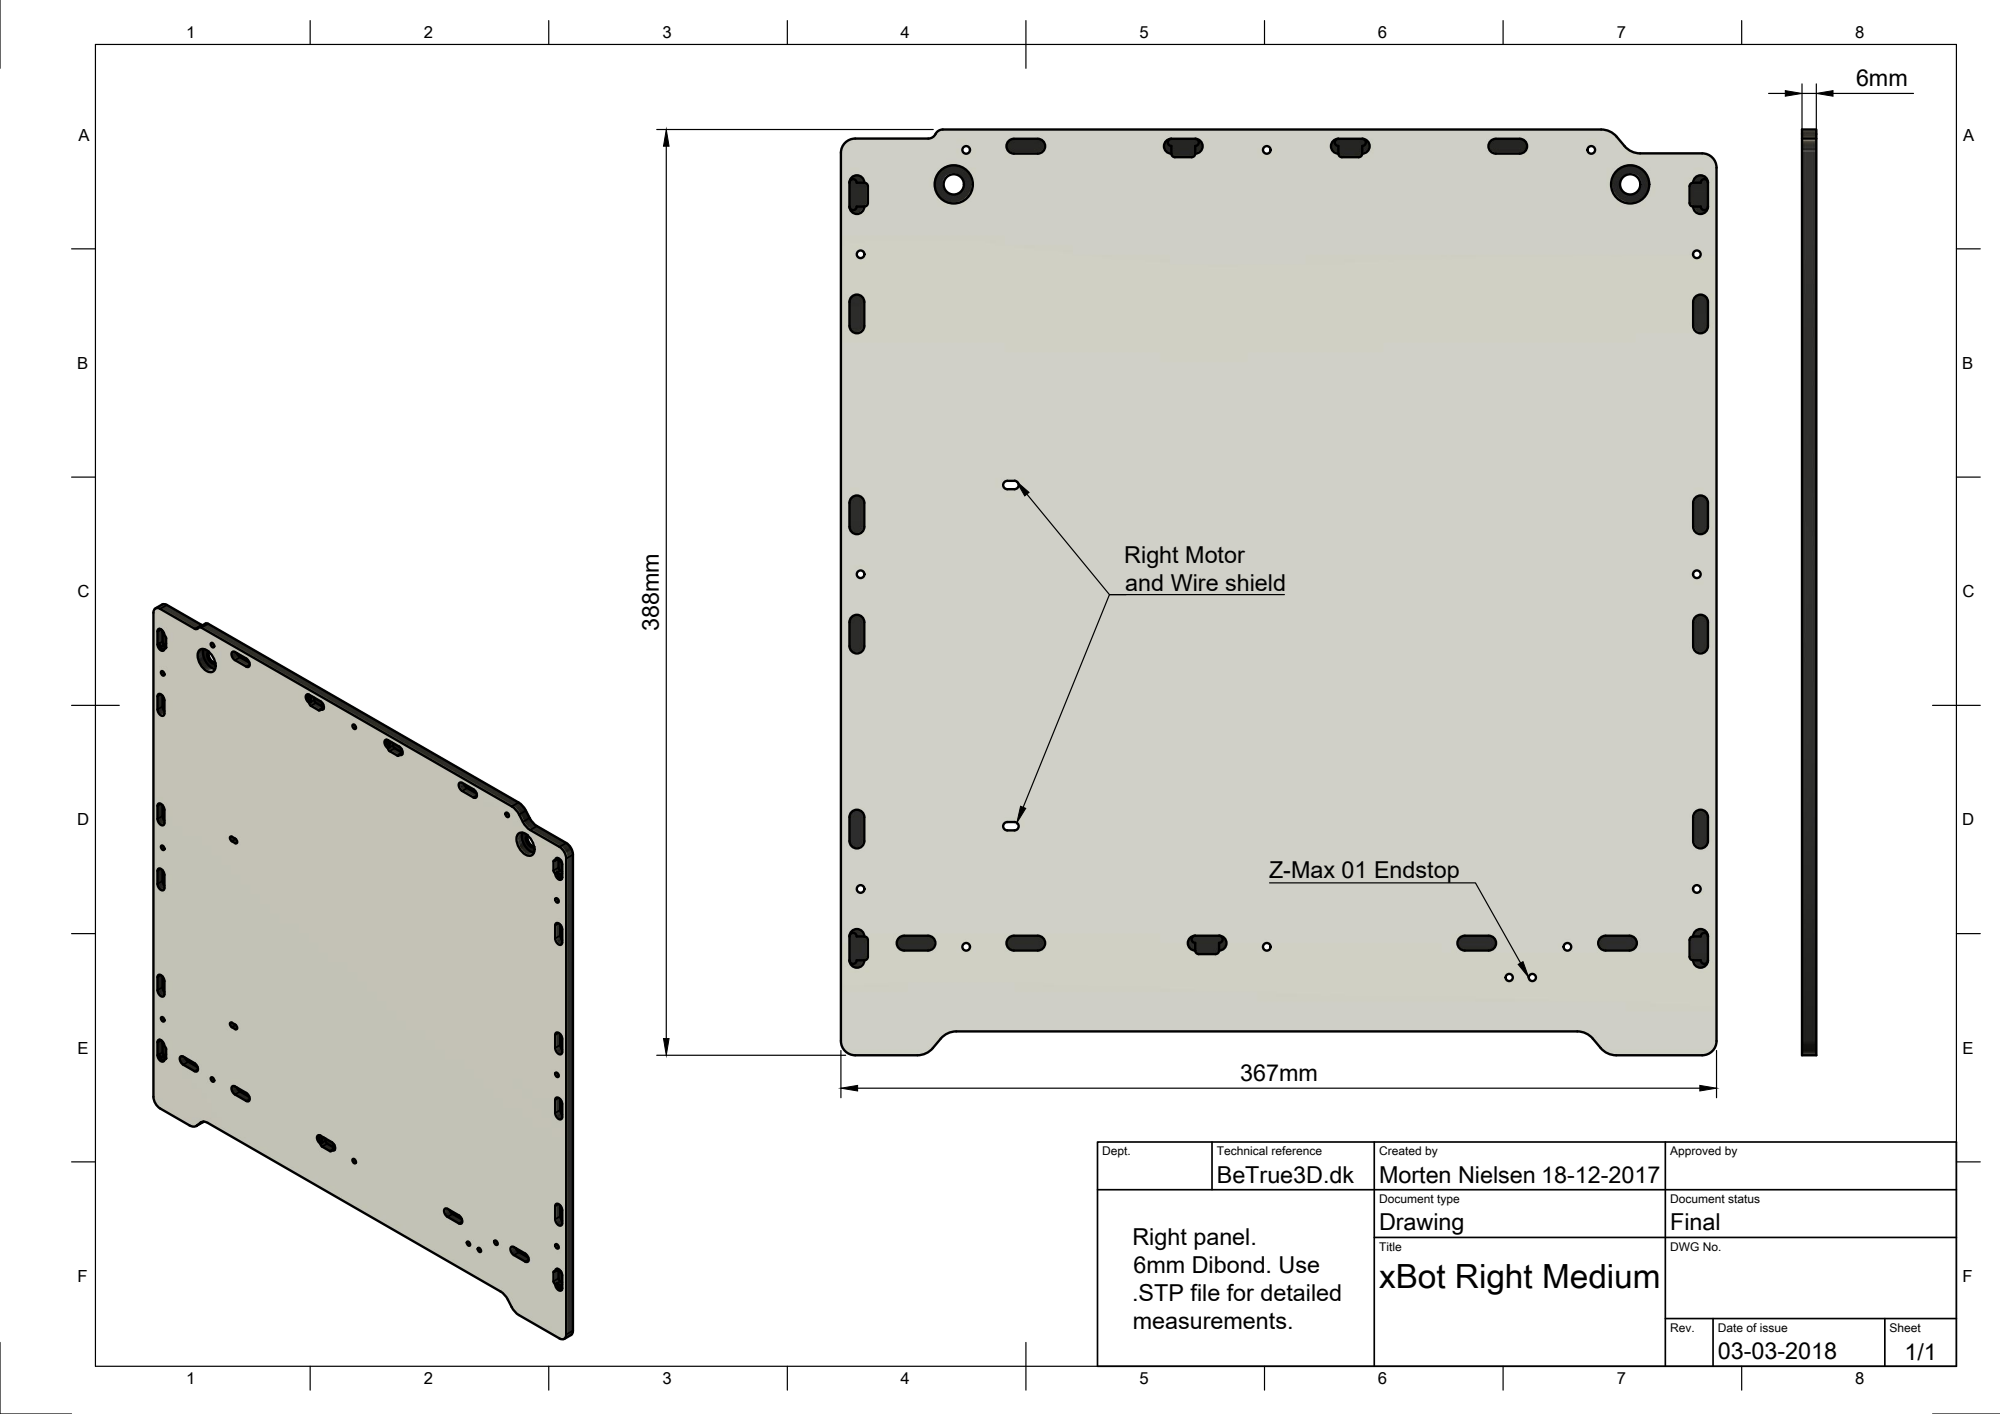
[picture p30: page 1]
BeTrue3D.dk; Morten Nielsen 388mm; Right Motor; Z-Max 01 Endstop

and Wire shield

Dept. | Technical reference | Created by 18-12-2017 | Approved by

Right panel. 6mm Dibond. Use .STP file for detailed measurements. | | Document type Drawing | Document status Final

Title xBot Right Medium | DWG No.

Rev. | Date of issue 03-03-2018 | Sheet 1/1

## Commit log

2017-12-20 Adjusted countersunk nut dimensions
2017-12-22 Allows for 48mm XY motors
    [Duet xBot Side Mount v1.stp, Duet xBot Side Mount v2.stp, MotorShield Left.stp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]
2017-12-22 Directory restructured
    [X-8mm-367mm rods x2.stp, Y-8mm 358mm rods x2.stp, Z-12mm rod-plates x2.stp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]
2017-12-24 Merry Christmas Release!
    [Chamber heater fanduct.stl, DuetDuex xBot Mounting x2.stl, Duex xBot Mounting x2.stp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]
2017-12-25 Added 6mm rods for carriage.
    [6mm rod Y axis 301mm.stp, 6mm rod X axis 327mm.stp]
2017-12-30 Small changes
    [Heatplate.stp, Z-12mm rod-plates - 4mm thick alu x2.stp, Z-8mm Rod-Plates - 4mm thick alux2.stp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]
2018-01-04 Added partial BOM
2018-01-07 Complete BOM w Cost
2018-01-29 Lots of minor and a few major changes. Fixes and added a bunch of printed parts.
    [10mm Spacer XY.stl, 15mm Spacer XY.stl, 1mm Spacer XY.stl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]
2018-01-30 Final modifications
    [Front LED.stp, MotorShield Left.stp, MotorShield right.stp]
2018-02-07 README
    In this directory you can find listings of various "other" items like dimensions and wiring of front LED, but also lenght and pin-layout of wiring harness to carriage and similar.
    I will be creating these files as I finish them up as "final" and measure them up.
    I can unveil the longest run of wireharness from the rear GX plugs up to carriage will be 100cm if you have configured your printer with the maxium distance possible, where you have a 3mm extruder pl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
    The 100cm is including the extra 5cm going into twisting the wires.
2018-02-09 Added dimensions for sensor offset and printhead settings
2018-02-12 Feb updates
    [10mm Spacer XY.stl, 15mm Spacer XY.stl, 1mm Spacer XY.stl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]
2018-02-13 Carriage wire length and connector definitions added
2018-02-14 More information
    [Hinge Door.stl, Hinge Frame.stl]
2018-03-02 Should be final
    [BeTrue3D xBot.stl, BeTrue3D.stl, Bed-Wire Relief.stl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]
2018-03-03 Motorshields optimization - Final
    [MotorShield x2.step]
